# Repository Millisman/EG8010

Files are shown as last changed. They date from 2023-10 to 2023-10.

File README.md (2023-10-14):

# EG8010
Collection of designs for the EG8010 (ASIC for single-phase SPWM control H-bridge)

# EG8010_A0
EG8010_A0 is the inverter version to replace EGS002. Uses TLP250 optical isolated drivers and a Totem-pole current amplifier to drive high gate capacitance MOSFET transistors. A four-pin Kelvin circuit is used for all connections.

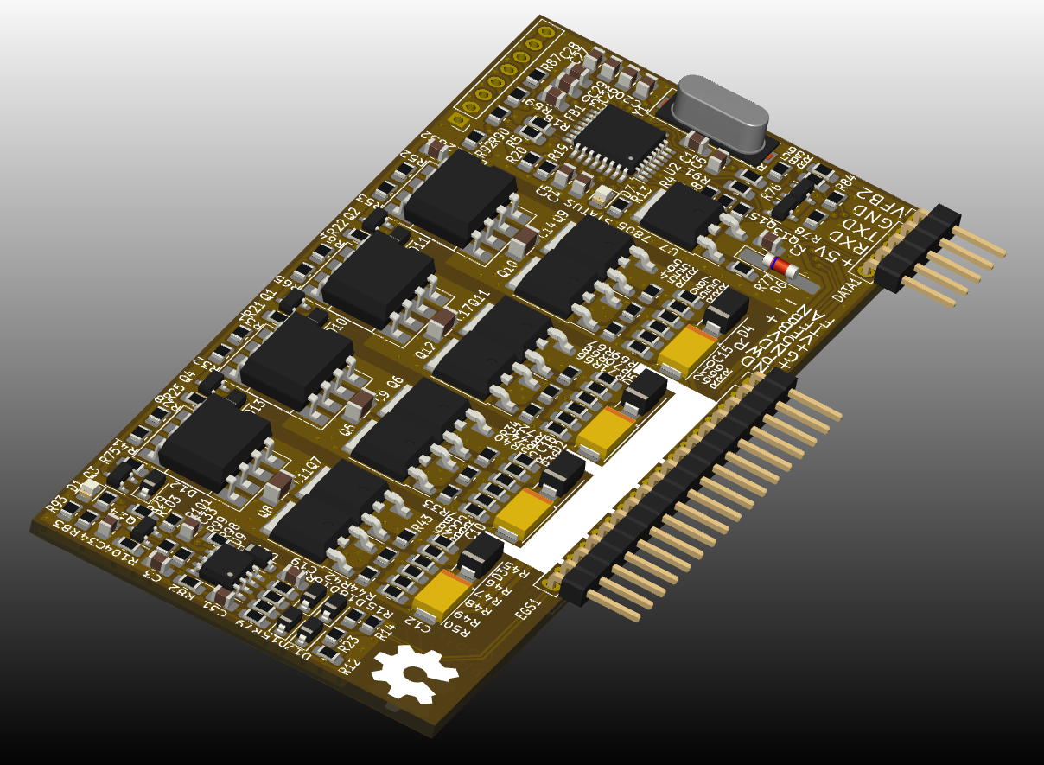
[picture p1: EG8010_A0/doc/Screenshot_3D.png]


The connection diagram has a minimum of parts. An external +5V power supply is not required if the 7805 is populated on board. The fan is controlled directly from the printed circuit board. Twisted wires are indicated by ovals. Please don't separate them.

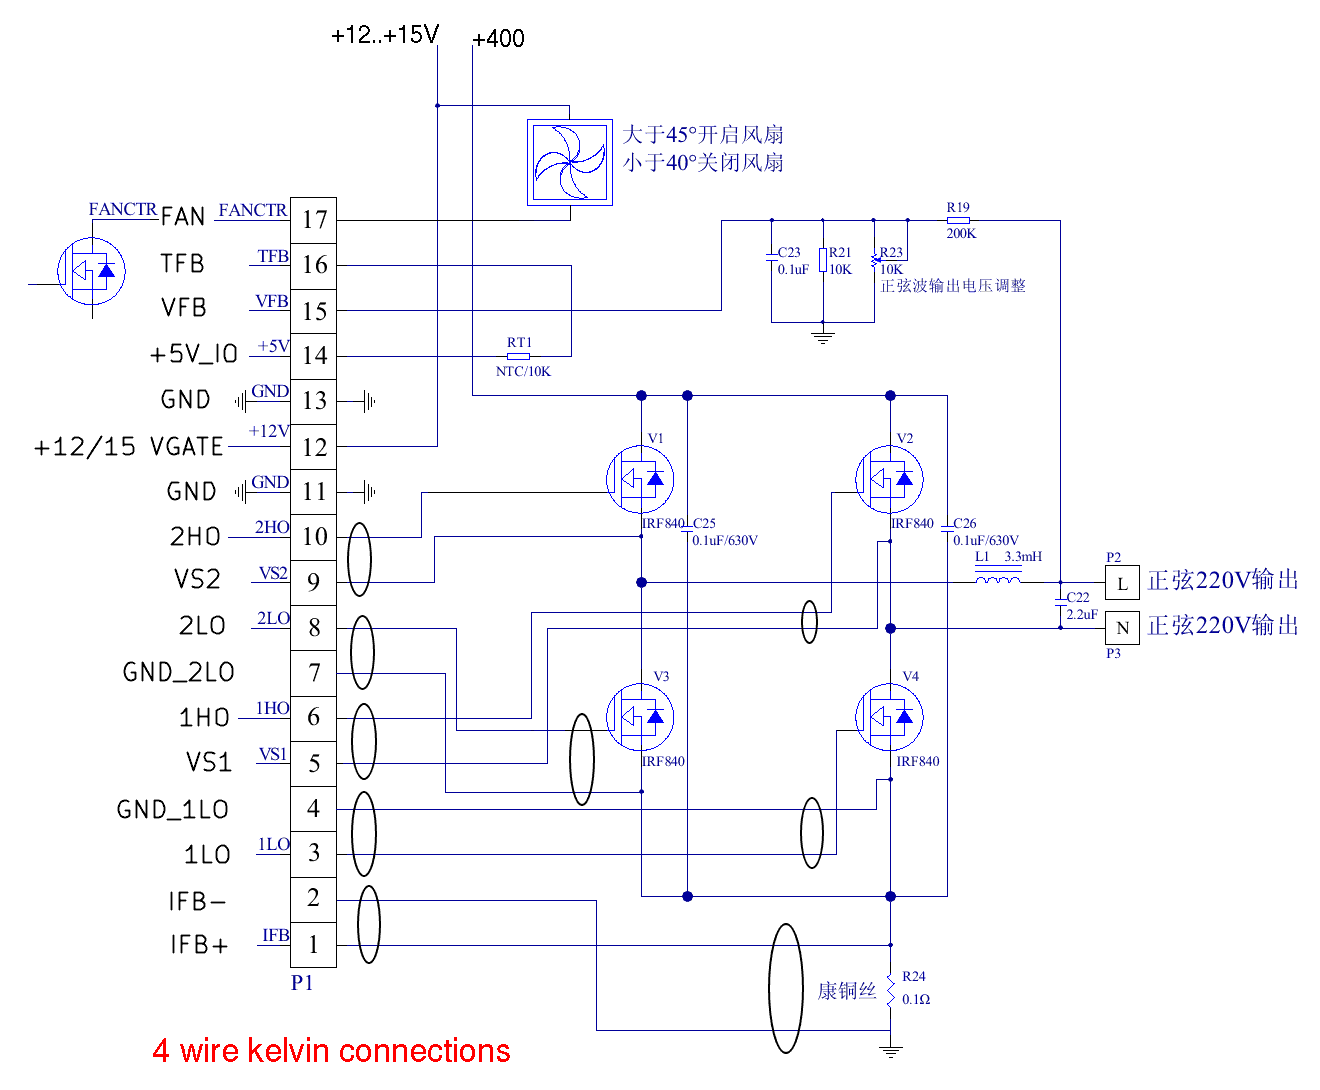
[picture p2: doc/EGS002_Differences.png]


# MIT License
Design is distributed under the terms of the MIT license.

You can use this project for personal and business.
You can make it and sell it.
You may modify this project as you see fit.
You are bound by the copyright.

NO WARRANTIES of any kind are given!

All actions are at your OWN RISK!

Copyright (c) 2023, Sergey Kostyanoy <contact@arduino.uno>

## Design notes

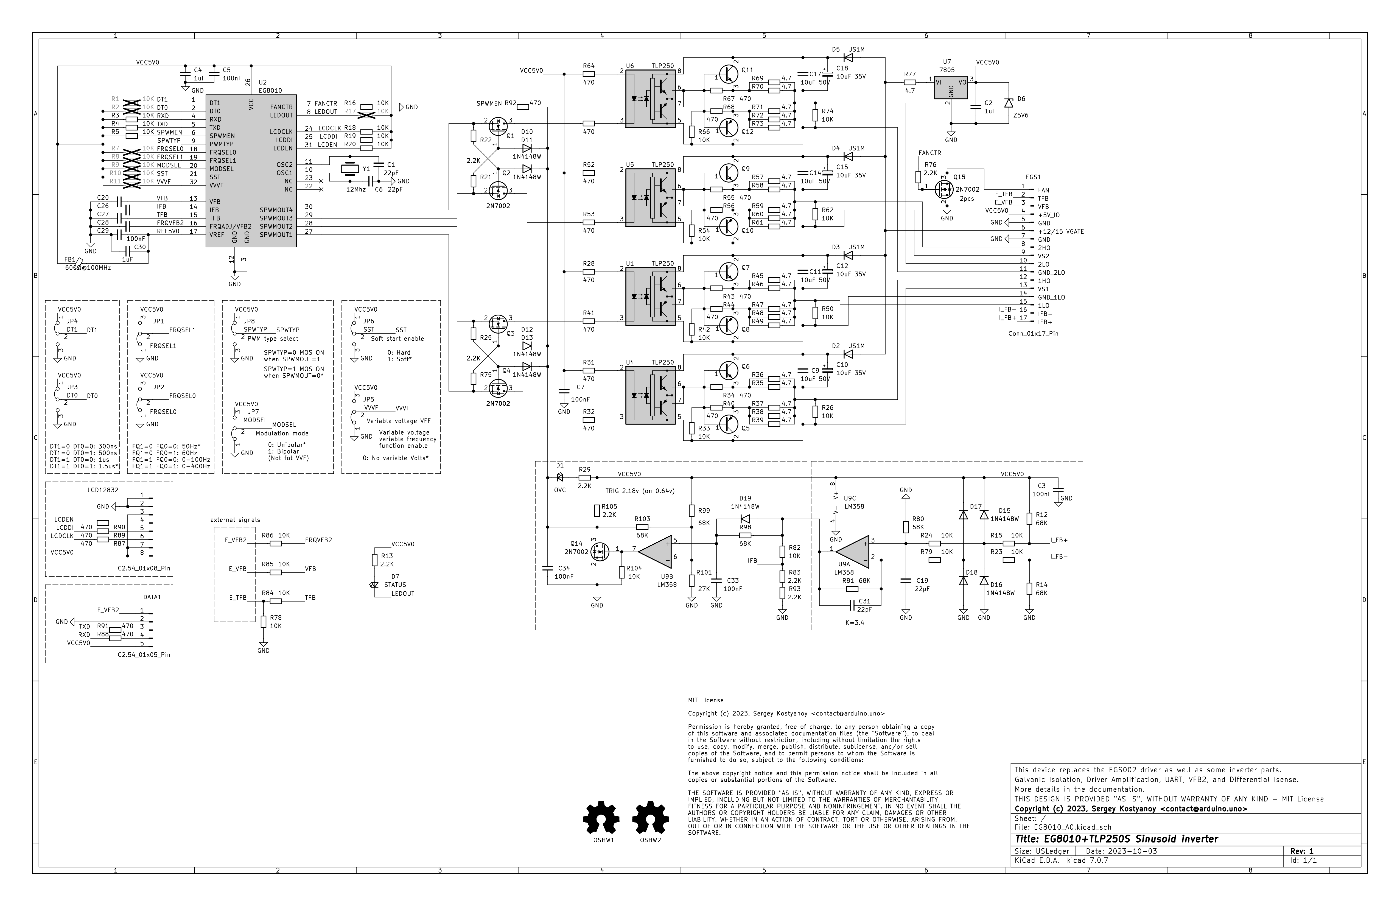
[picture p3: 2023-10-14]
EG8010_A0/Schematic_EG8010_A0.png

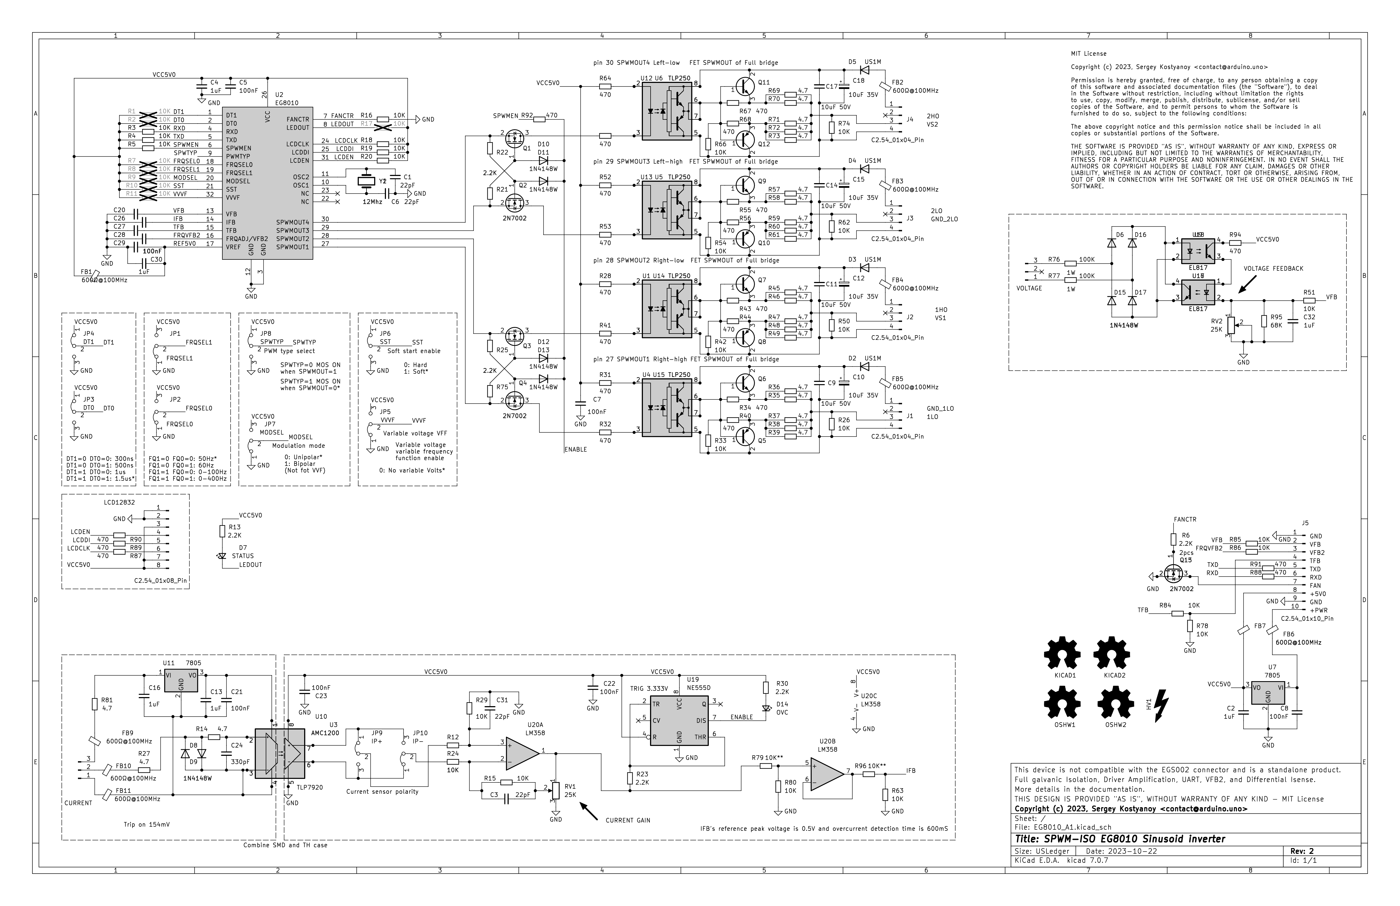
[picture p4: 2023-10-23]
EG8010_A1/Schematic_EG8010_A1.png

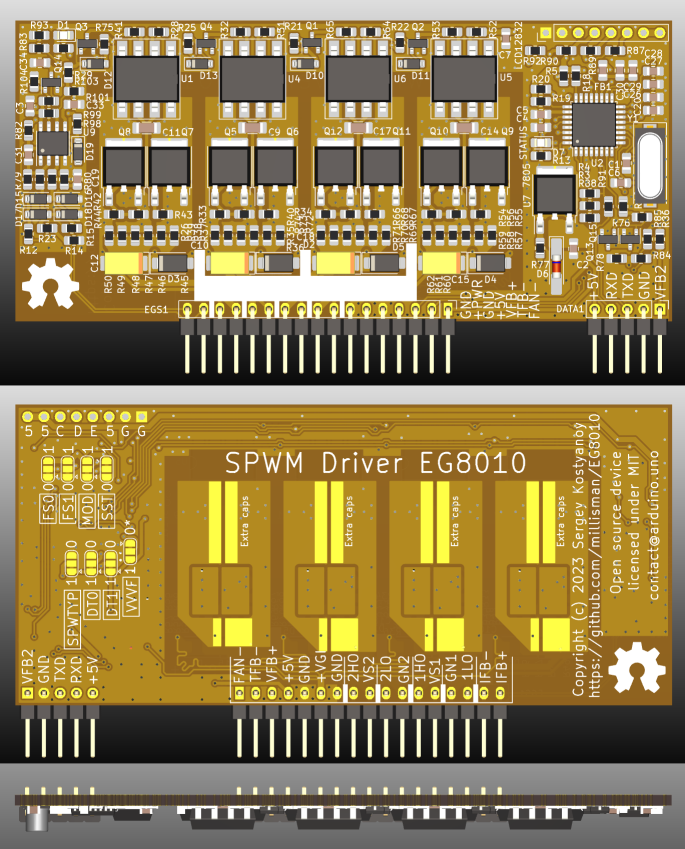
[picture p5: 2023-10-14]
EG8010_A0/doc/Screenshot_all.png

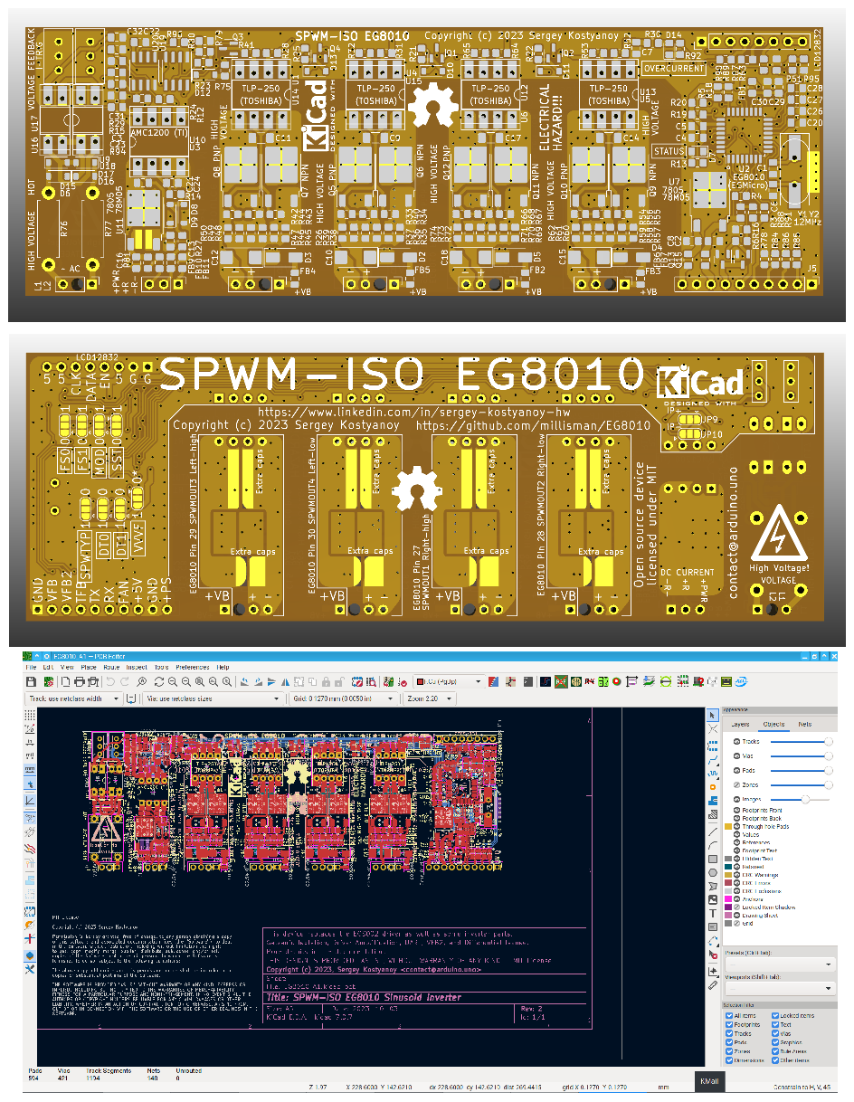
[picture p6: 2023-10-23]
EG8010_A1/doc/Screenshot_2D.png

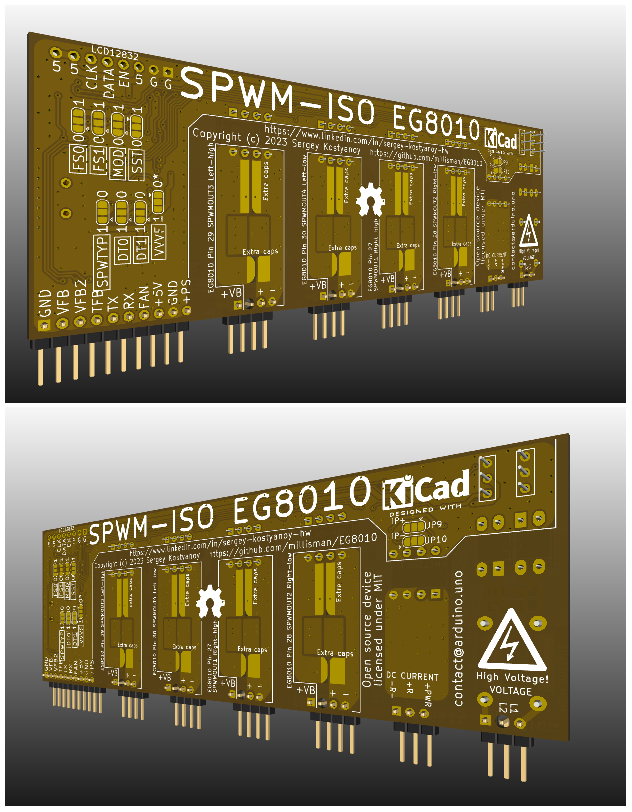
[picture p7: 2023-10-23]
EG8010_A1/doc/Screenshot_B.png

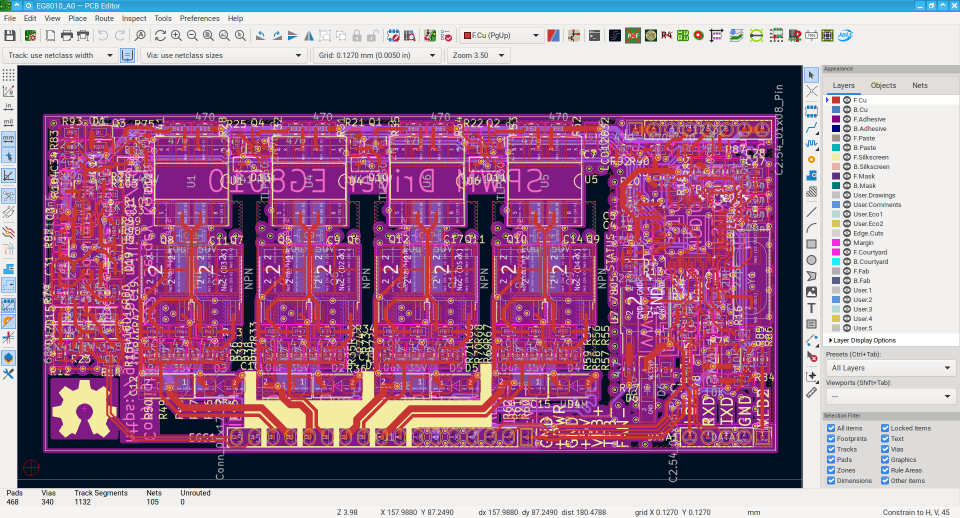
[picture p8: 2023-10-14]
EG8010_A0/doc/Screenshot_KiCAD.png

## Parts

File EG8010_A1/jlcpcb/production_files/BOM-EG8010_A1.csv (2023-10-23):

Comment | Designator | Footprint | LCSC
EL817 | U16,U9 | DIP-4_W8.89mm_SMDSocket_LongPads | C106900
NPN | Q11,Q6,Q7,Q9 | TO-252-2 | C138779
PNP | Q10,Q12,Q5,Q8 | TO-252-2 | C138783
10K | R12,R15,R16,R18,R19,R20,R24,R26,R29,R3,R33,R4,R42,R5,R50,R51,R54,R62,R63,R66,R74,R78,R79,R80,R84,R85,R86,R96 | R_0805_2012Metric_Pad1.20x1.40mm_HandSolder | C17414
2.2K | R13,R21,R22,R23,R25,R30,R6,R75 | R_0805_2012Metric_Pad1.20x1.40mm_HandSolder | C17520
4.7 | R14,R27,R35,R36,R37,R38,R39,R45,R46,R47,R48,R49,R57,R58,R59,R60,R61,R69,R70,R71,R72,R73,R81 | R_0805_2012Metric_Pad1.20x1.40mm_HandSolder | C17675
470 | R28,R31,R32,R34,R40,R41,R43,R44,R52,R53,R55,R56,R64,R65,R67,R68,R87,R88,R89,R90,R91,R92,R94 | R_0805_2012Metric_Pad1.20x1.40mm_HandSolder | C17710
68K | R95 | R_0805_2012Metric_Pad1.20x1.40mm_HandSolder | C17801
22pF | C1,C3,C31,C6 | C_0805_2012Metric_Pad1.18x1.45mm_HandSolder | C1804
EL817 | U17,U18 | DIP-4_W7.62mm_Socket_LongPads | C181890
TLP250 | U1,U4,U5,U6 | DIP-8_W8.89mm_SMDSocket_LongPads | C2802426
100nF | C20,C21,C22,C23,C24,C26,C27,C28,C29,C5,C7,C8 | C_0805_2012Metric_Pad1.18x1.45mm_HandSolder | C28233
1uF | C13,C16,C2,C30,C32,C4 | C_0805_2012Metric_Pad1.18x1.45mm_HandSolder | C28323
600Ω@100MHz | FB1,FB10,FB11,FB2,FB3,FB4,FB5,FB6,FB7,FB9 | C_0805_2012Metric_Pad1.18x1.45mm_HandSolder | C2858468
10uF 50V | C11,C14,C17,C9 | C_1206_3216Metric_Pad1.33x1.80mm_HandSolder | C303950
AMC1200 | U3 | DIP-8_W8.89mm_SMDSocket_LongPads | C39673
TLP250 | U12,U13,U14,U15 | DIP-8_W7.62mm_Socket | C4078
US1M | D2,D3,D4,D5 | D_SMA | C412437
10uF 35V | C10,C12,C15,C18 | CP_EIA-6032-15_Kemet-U_Pad2.25x2.35mm_HandSolder | C435847
25K | RV1,RV2 | Potentiometer_Bourns_3296W_Vertical | C55264
7805 | U11,U7 | TO-252-2 | C58069
12Mhz | Y1 | Crystal_SMD_HC49-SD | C6555079
100K | R76,R77 | R_Axial_DIN0411_L9.9mm_D3.6mm_P12.70mm_Horizontal | C714116
NE555D | U19 | SOIC-8_3.9x4.9mm_P1.27mm | C7593
LM358 | U20 | SOIC-8_3.9x4.9mm_P1.27mm | C7950
1N4148W | D10,D11,D12,D13,D15,D16,D17,D6,D8,D9 | D_SOD-123 | C81598
EG8010 | U2 | LQFP-32_7x7mm_P0.8mm | C81683
OVC | D14,D7 | LED_0805_2012Metric_Pad1.15x1.40mm_HandSolder | C84256
2N7002 | Q1,Q13,Q15,Q2,Q3,Q4 | SOT-23 | C8545
VOLTAGE | J6 | PinHeader_1x03_P2.54mm_Vertical
Conn_01x10_Pin | J5 | PinHeader_1x10_P2.54mm_Vertical
CURRENT | J7 | PinHeader_1x03_P2.54mm_Vertical
AMC1200 | U10 | DIP-8_W7.62mm_Socket
High Voltage! | HV1 | High_Voltage_Logo_10mm

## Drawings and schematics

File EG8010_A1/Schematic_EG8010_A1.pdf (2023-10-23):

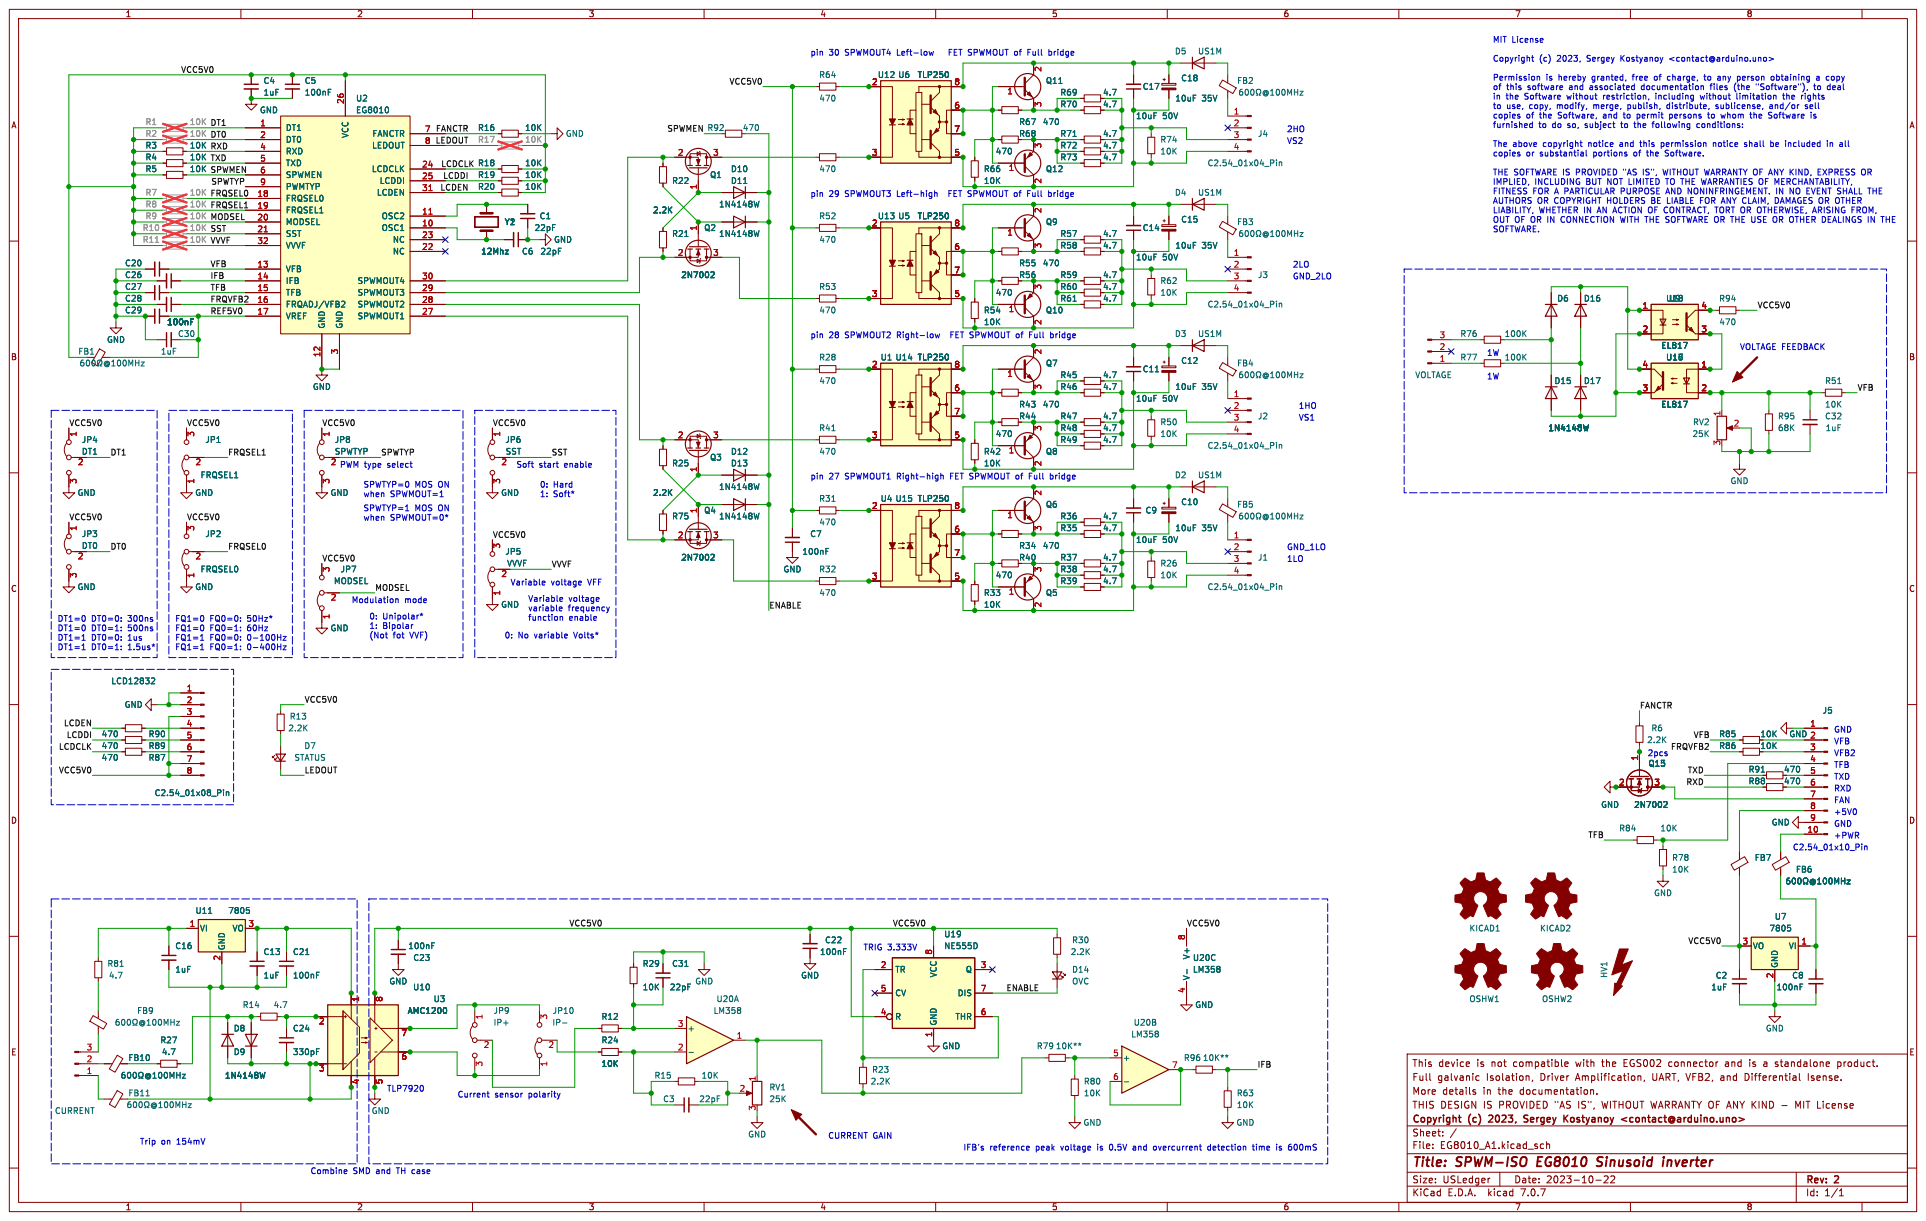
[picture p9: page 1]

IMPLIED, INCLUDING BUT NOT LIMITED TO THE WARRANTIES OF MERCHANTABILITY, FITNESS FOR A PARTICULAR PURPOSE AND NONINFRINGEMENT. IN NO EVENT SHALL THE

AUTHORS OR COPYRIGHT HOLDERS BE LIABLE FOR ANY CLAIM, DAMAGES OR OTHER
LIABILITY, WHETHER IN AN ACTION OF CONTRACT, TORT OR OTHERWISE, ARISING FROM, OUT OF OR IN CONNECTION WITH THE SOFTWARE OR THE USE OR OTHER DEALINGS IN THE

3 JP6 SST GND GND GND

when SPWMOUT=1 SPWTYP=1 MOS ON

TRIG 3.333V Current sensor polarity

Combine SMD and TH case

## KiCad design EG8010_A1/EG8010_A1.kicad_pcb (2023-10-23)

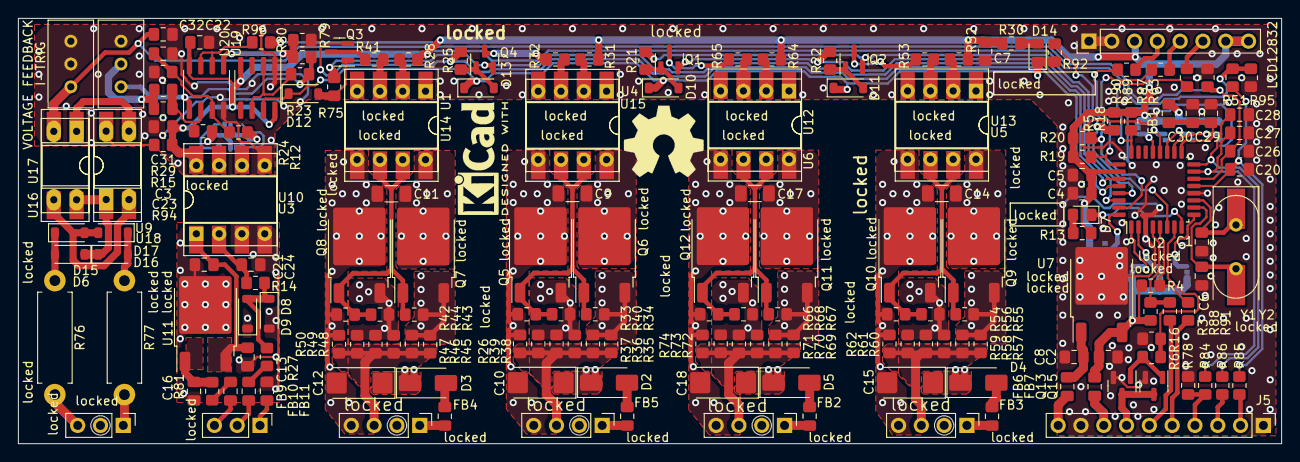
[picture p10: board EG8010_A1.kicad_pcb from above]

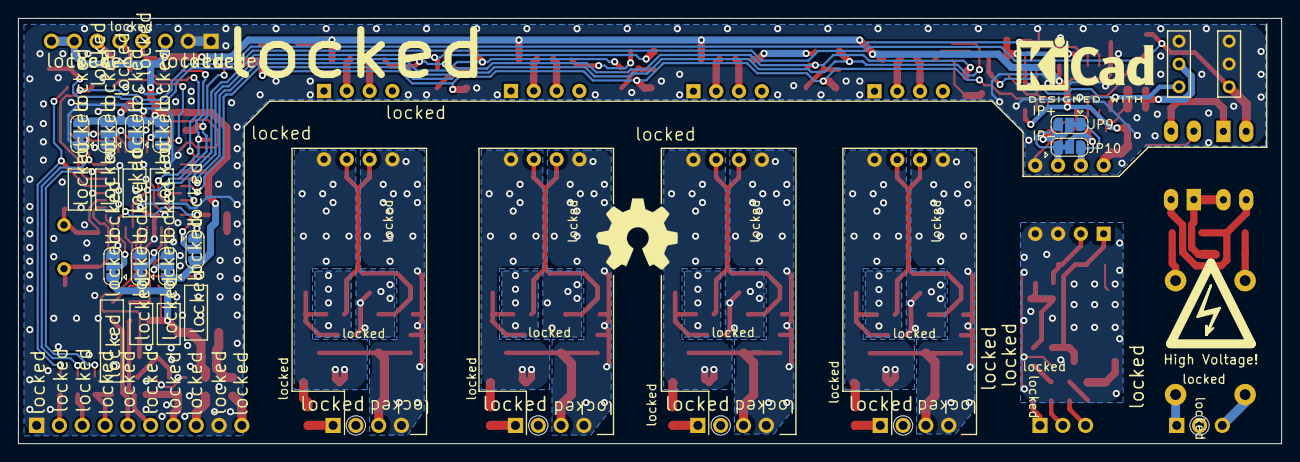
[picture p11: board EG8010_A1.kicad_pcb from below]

Board: 2 copper layers, 140.7 x 47.4 mm, 201 parts (13 on the bottom side), 123 nets.

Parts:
C1, C3, C6, C31: 22pF; C_0805_2012Metric_Pad1.18x1.45mm_HandSolder
C2, C4, C13, C16, C30, C32: 1uF; C_0805_2012Metric_Pad1.18x1.45mm_HandSolder
C5, C7, C8, C20, C21, C22, C23, C26, C27, C28, C29: 100nF; C_0805_2012Metric_Pad1.18x1.45mm_HandSolder
C9, C11, C14, C17: 10uF 50V; C_1206_3216Metric_Pad1.33x1.80mm_HandSolder
C10, C12, C15, C18: 10uF 35V; CP_EIA-6032-15_Kemet-U_Pad2.25x2.35mm_HandSolder
C24: 330pF; C_0805_2012Metric_Pad1.18x1.45mm_HandSolder
D2, D3, D4, D5: US1M; D_SMA
D6, D8, D9, D10, D11, D12, D13, D15, D16, D17: 1N4148W; D_SOD-123
D7: STATUS; LED_0805_2012Metric_Pad1.15x1.40mm_HandSolder
D14: OVC; LED_0805_2012Metric_Pad1.15x1.40mm_HandSolder
FB1, FB2, FB3, FB4, FB5, FB6, FB7, FB9, FB10, FB11: 600Ω@100MHz; C_0805_2012Metric_Pad1.18x1.45mm_HandSolder
HV1: High Voltage!; High_Voltage_Logo_10mm
J1, J2, J3, J4: C2.54_01x04_Pin; PinHeader_1x04_P2.54mm_Vertical
J5: Conn_01x10_Pin; PinHeader_1x10_P2.54mm_Vertical
J6: VOLTAGE; PinHeader_1x03_P2.54mm_Vertical
J7: CURRENT; PinHeader_1x03_P2.54mm_Vertical
JP1: FRQSEL1; SolderJumper-3_P1.3mm_Bridged12_RoundedPad1.0x1.5mm
JP2: FRQSEL0; SolderJumper-3_P1.3mm_Bridged12_RoundedPad1.0x1.5mm
JP3: DT0; SolderJumper-3_P1.3mm_Bridged12_RoundedPad1.0x1.5mm
JP4: DT1; SolderJumper-3_P1.3mm_Bridged12_RoundedPad1.0x1.5mm
JP5: VVVF; SolderJumper-3_P1.3mm_Bridged12_RoundedPad1.0x1.5mm
JP6: SST; SolderJumper-3_P1.3mm_Bridged12_RoundedPad1.0x1.5mm
JP7: MODSEL; SolderJumper-3_P1.3mm_Bridged12_RoundedPad1.0x1.5mm
JP8: SPWTYP; SolderJumper-3_P1.3mm_Bridged12_RoundedPad1.0x1.5mm
JP9: IP+; SolderJumper-3_P1.3mm_Bridged12_RoundedPad1.0x1.5mm
JP10: IP-; SolderJumper-3_P1.3mm_Bridged12_RoundedPad1.0x1.5mm
KICAD1: KiCad-Logo2_6mm_SilkScreen
KICAD2: KiCad-Logo2_5mm_SilkScreen
LCD12832: C2.54_01x08_Pin; PinHeader_1x08_P2.54mm_Vertical
OSHW1, OSHW2: Logo_Open_Hardware_Small; OSHW-Symbol_8.9x8mm_SilkScreen
Q1, Q2, Q3, Q4, Q13, Q15: 2N7002; SOT-23
Q5, Q8, Q10, Q12: PNP; TO-252-2
Q6, Q7, Q9, Q11: NPN; TO-252-2
R3, R4, R5, R12, R15, R16, R18, R19, R20, R24, R26, R29, R33, R42, R50, R51, R54, R62, R63, R66, R74, R78, R80, R84, R85, R86: 10K; R_0805_2012Metric_Pad1.20x1.40mm_HandSolder
R6, R13, R21, R22, R23, R25, R30, R75: 2.2K; R_0805_2012Metric_Pad1.20x1.40mm_HandSolder
R14, R27, R35, R36, R37, R38, R39, R45, R46, R47, R48, R49, R57, R58, R59, R60, R61, R69, R70, R71, R72, R73, R81: 4.7; R_0805_2012Metric_Pad1.20x1.40mm_HandSolder
R28, R31, R32, R34, R40, R41, R43, R44, R52, R53, R55, R56, R64, R65, R67, R68, R87, R88, R89, R90, R91, R92, R94: 470; R_0805_2012Metric_Pad1.20x1.40mm_HandSolder
R76, R77: 100K; R_Axial_DIN0411_L9.9mm_D3.6mm_P12.70mm_Horizontal
R79, R96: 10K**; R_0805_2012Metric_Pad1.20x1.40mm_HandSolder
R95: 68K; R_0805_2012Metric_Pad1.20x1.40mm_HandSolder
RV1, RV2: 25K; Potentiometer_Bourns_3296W_Vertical
U1, U4, U5, U6: TLP250; DIP-8_W8.89mm_SMDSocket_LongPads
U2: EG8010; LQFP-32_7x7mm_P0.8mm
U3: AMC1200; DIP-8_W8.89mm_SMDSocket_LongPads
U7, U11: 7805; TO-252-2
U9, U16: EL817; DIP-4_W8.89mm_SMDSocket_LongPads
U10: AMC1200; DIP-8_W7.62mm_Socket
U12, U13, U14, U15: TLP250; DIP-8_W7.62mm_Socket
U17, U18: EL817; DIP-4_W7.62mm_Socket_LongPads
U19: NE555D; SOIC-8_3.9x4.9mm_P1.27mm
U20: LM358; SOIC-8_3.9x4.9mm_P1.27mm
Y1: 12Mhz; Crystal_SMD_HC49-SD
Y2: 12Mhz; Crystal_HC49-4H_Vertical

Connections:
/DT0: JP3.2 (C), U2.2 (DT0)
/DT1: JP4.2 (C), U2.1 (DT1)
/ENABLE: D10.1 (K), D11.1 (K), D12.1 (K), D13.1 (K), D14.1 (K), R92.2, U19.7 (DIS)
/FANCTR: R6.1, R16.2, U2.7 (FANCTR)
/FRQSEL0: JP2.2 (C), U2.18 (FRQSEL0)
/FRQSEL1: JP1.2 (C), U2.19 (FRQSEL1)
/FRQVFB2: C28.1, R86.1, U2.16 (FRQADJ/VFB2)
/IFB: C26.1, R63.2, R96.1, U2.14 (IFB)
/LCDCLK: R18.2, R87.2, U2.24 (LCDCLK)
/LCDDI: R19.2, R89.2, U2.25 (LCDDI)
/LCDEN: R20.2, R90.2, U2.31 (LCDEN)
/LEDOUT: D7.1 (K), U2.8 (LEDOUT)
/MODSEL: JP7.2 (C), U2.20 (MODSEL)
/REF5V0: C29.1, C30.2, FB1.1, U2.17 (VREF)
/RXD: R3.1, R88.2, U2.4 (RXD)
/SPWMEN: R5.1, R92.1, U2.6 (SPWMEN)
/SPWTYP: JP8.2 (C), U2.9 (PWMTYP)
/SST: JP6.2 (C), U2.21 (SST)
/TFB: C27.1, R84.1, U2.15 (TFB)
/TXD: R4.1, R91.2, U2.5 (TXD)
/VCC5V0: C2.1, C4.1, C5.1, C7.2, C22.2, C23.1, FB1.2, FB7.2, JP1.3 (B), JP2.3 (B), JP3.1 (A), JP4.1 (A), JP5.3 (B), JP6.1 (A), JP7.3 (B), JP8.1 (A), LCD12832.3, LCD12832.7, LCD12832.8, R3.2, R4.2, R5.2, R13.2, R18.1, R19.1, R20.1, R28.1, R30.2, R31.1, R52.1, R64.1, R94.2, U2.26 (VCC), U3.8 (VDD2), U7.3 (VO), U10.8 (VDD2), U19.4 (R), U19.8 (VCC), U20.8 (V+)
/VFB: C20.1, R51.2, R85.1, U2.13 (VFB)
/VVVF: JP5.2 (C), U2.32 (VVVF)
GND: C1.1, C2.2, C4.2, C5.2, C6.1, C7.1, C8.2, C20.2, C22.1, C23.2, C26.2, C27.2, C28.2, C29.2, C30.1, C31.2, C32.2, J5.1, J5.9, JP1.1 (A), JP2.1 (A), JP3.3 (B), JP4.3 (B), JP5.1 (A), JP6.3 (B), JP7.1 (A), JP8.3 (B), LCD12832.1, LCD12832.2, Q13.2 (S), Q15.2 (S), R16.1, R29.2, R63.1, R78.1, R80.1, R95.2, RV1.3, RV2.2, RV2.3, U2.3 (GND), U2.12 (GND), U3.5 (GND2), U7.2 (GND), U10.5 (GND2), U19.1 (GND), U20.4 (V-)
unnamed: C3.2, R15.1, RV1.2
unnamed: C32.1, R51.1, R95.1, RV2.1, U16.2, U17.2
unnamed: D2.2 (A), FB5.2
unnamed: C9.2, C10.1, D2.1 (K), Q6.2 (C), U4.8 (VCC), U15.8 (VCC)
unnamed: D3.2 (A), FB4.2
unnamed: C11.2, C12.1, D3.1 (K), Q7.2 (C), U1.8 (VCC), U14.8 (VCC)
unnamed: D4.2 (A), FB3.2
unnamed: C14.2, C15.1, D4.1 (K), Q9.2 (C), U5.8 (VCC), U13.8 (VCC)
unnamed: D5.2 (A), FB2.2
unnamed: C17.2, C18.1, D5.1 (K), Q11.2 (C), U6.8 (VCC), U12.8 (VCC)
unnamed: D7.2 (A), R13.1
unnamed: C13.2, C16.2, C21.2, C24.2, D8.2 (A), D9.1 (K), FB11.1, U3.3 (IN-), U3.4 (GND1), U10.3 (IN-), U10.4 (GND1), U11.2 (GND)
unnamed: D8.1 (K), D9.2 (A), R14.1, R27.2
unnamed: D10.2 (A), Q1.1 (G), R21.2
unnamed: D11.2 (A), Q2.1 (G), R22.1
unnamed: D12.2 (A), Q3.1 (G), R75.2
unnamed: D13.2 (A), Q4.1 (G), R25.1
unnamed: D14.2 (A), R30.1
unnamed: D15.2 (A), D17.2 (A), U9.2, U16.3, U17.3, U18.2
unnamed: D6.2 (A), D15.1 (K), R76.2
unnamed: D16.2 (A), D17.1 (K), R77.2
unnamed: D6.1 (K), D16.1 (K), U9.1, U16.4, U17.4, U18.1
unnamed: FB9.1, R81.2
unnamed: FB10.1, R27.1
unnamed: FB5.1, J1.1
unnamed: J1.3, R26.2, R35.2, R36.2, R37.2, R38.2, R39.2
unnamed: C9.1, C10.2, J1.4, Q5.2 (C), R26.1, R33.1, U4.5 (VEE), U15.5 (VEE)
unnamed: FB4.1, J2.1
unnamed: J2.3, R45.2, R46.2, R47.2, R48.2, R49.2, R50.2
unnamed: C11.1, C12.2, J2.4, Q8.2 (C), R42.1, R50.1, U1.5 (VEE), U14.5 (VEE)
unnamed: FB3.1, J3.1
unnamed: J3.3, R57.2, R58.2, R59.2, R60.2, R61.2, R62.2
unnamed: C14.1, C15.2, J3.4, Q10.2 (C), R54.1, R62.1, U5.5 (VEE), U13.5 (VEE)
unnamed: FB2.1, J4.1
unnamed: J4.3, R69.2, R70.2, R71.2, R72.2, R73.2, R74.2
unnamed: C17.1, C18.2, J4.4, Q12.2 (C), R66.1, R74.1, U6.5 (VEE), U12.5 (VEE)
unnamed: J5.2, R85.2
unnamed: J5.3, R86.2
unnamed: J5.4, R78.2, R84.2
unnamed: J5.5, R91.1
unnamed: J5.6, R88.1
unnamed: J5.7, Q13.3 (D), Q15.3 (D)
unnamed: FB7.1, J5.8
unnamed: FB6.1, J5.10
unnamed: J6.1, R77.1
unnamed: J6.3, R76.1
unnamed: FB11.2, J7.1
unnamed: FB10.2, J7.2
unnamed: FB9.2, J7.3
unnamed: JP9.2 (C), R12.2
unnamed: JP9.3 (B), JP10.1 (A), U3.6 (OUT-), U10.6 (OUT-)
unnamed: JP9.1 (A), JP10.3 (B), U3.7 (OUT+), U10.7 (OUT+)
unnamed: JP10.2 (C), R24.2
unnamed: LCD12832.4, R90.1
unnamed: LCD12832.5, R89.1
unnamed: LCD12832.6, R87.1
unnamed: Q1.3 (D), R65.1
unnamed: Q1.2 (S), R22.2, U2.30 (SPWMOUT4)
unnamed: Q2.3 (D), R53.1
unnamed: Q2.2 (S), R21.1, U2.29 (SPWMOUT3)
unnamed: Q3.3 (D), R41.1
unnamed: Q3.2 (S), R25.2, U2.28 (SPWMOUT2)
unnamed: Q4.3 (D), R32.1
unnamed: Q4.2 (S), R75.1, U2.27 (SPWMOUT1)
unnamed: Q5.1 (B), Q6.1 (B), R33.2, R34.1, R40.1, U4.6 (VO), U4.7 (VO), U15.6 (VO), U15.7 (VO)
unnamed: Q5.3 (E), R37.1, R38.1, R39.1, R40.2
unnamed: Q6.3 (E), R34.2, R35.1, R36.1
unnamed: Q7.1 (B), Q8.1 (B), R42.2, R43.1, R44.1, U1.6 (VO), U1.7 (VO), U14.6 (VO), U14.7 (VO)
unnamed: Q7.3 (E), R43.2, R45.1, R46.1
unnamed: Q8.3 (E), R44.2, R47.1, R48.1, R49.1
unnamed: Q9.3 (E), R55.2, R57.1, R58.1
unnamed: Q9.1 (B), Q10.1 (B), R54.2, R55.1, R56.1, U5.6 (VO), U5.7 (VO), U13.6 (VO), U13.7 (VO)
unnamed: Q10.3 (E), R56.2, R59.1, R60.1, R61.1
unnamed: Q11.1 (B), Q12.1 (B), R66.2, R67.1, R68.1, U6.6 (VO), U6.7 (VO), U12.6 (VO), U12.7 (VO)
unnamed: Q11.3 (E), R67.2, R69.1, R70.1
unnamed: Q12.3 (E), R68.2, R71.1, R72.1, R73.1
unnamed: Q13.1 (G), Q15.1 (G), R6.2
unnamed: R23.1, R79.2, RV1.1, U20.1
unnamed: R94.1, U9.4, U18.4
unnamed: R28.2, U1.2 (A), U14.2 (A)
unnamed: R41.2, U1.3 (C), U14.3 (C)
unnamed: C6.2, U2.10 (OSC1), Y1.2, Y2.2
unnamed: C1.2, U2.11 (OSC2), Y1.1, Y2.1
unnamed: C8.1, FB6.2, U7.1 (VI)
unnamed: C24.1, R14.2, U3.2 (IN+), U10.2 (IN+)
unnamed: C13.1, C21.1, U3.1 (VDD1), U10.1 (VDD1), U11.3 (VO)
unnamed: C16.1, R81.1, U11.1 (VI)
unnamed: R64.2, U6.2 (A), U12.2 (A)
unnamed: R65.2, U6.3 (C), U12.3 (C)
unnamed: R52.2, U5.2 (A), U13.2 (A)
unnamed: R53.2, U5.3 (C), U13.3 (C)
unnamed: R31.2, U4.2 (A), U15.2 (A)
unnamed: R32.2, U4.3 (C), U15.3 (C)
unnamed: U9.3, U16.1, U17.1, U18.3
unnamed: R23.2, U19.2 (TR), U19.6 (THR)
unnamed: C31.1, R12.1, R29.1, U20.3 (+)
unnamed: C3.1, R15.2, R24.1, U20.2 (-)
unnamed: R79.1, R80.2, U20.5 (+)
unnamed: R96.2, U20.6 (-), U20.7

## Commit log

2023-10-14 Add files via upload
    4 wire kelvin connection VS standard EGS002
2023-10-23 Added rev A1 (SPWM ISO)
    [BOM-EG8010_A1.csv, EG8010_A1.kicad_pcb, EG8010_A1.kicad_sch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]

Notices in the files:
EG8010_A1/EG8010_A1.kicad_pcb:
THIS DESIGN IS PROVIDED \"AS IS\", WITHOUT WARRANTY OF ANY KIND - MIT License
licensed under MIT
